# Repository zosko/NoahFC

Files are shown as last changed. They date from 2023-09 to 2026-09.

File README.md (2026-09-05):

# NoahFC
Open Hardware for Smarter Flight

Modular, open-source flight controller with integrated BEC and ESC designs. Build, customize, and fly freely.

#### Based low cost Atmega328 based Flight Controller with necessary features.

# Electronic used
- Flight Controller - [NoahFC](https://github.com/zosko/NoahFC)
- ESC Controller - [NoahESC](https://github.com/zosko/NoahESC)
- BEC - [NoahBEC](https://github.com/zosko/NoahBEC)
- Receiver - (TBS Nano)
- Plane - (ZOHD Drift)
- Camera
- VTX Transmitter

### Features
- [X] **PPM**
- [X] **GPS**
- [X] **Manual mode**
- [X] **Stable mode**
- [X] Return to home
- [X] **OSD**

### Used Pins
Arduino | Component | Arduino | Component
--------|----------|---------|---------
D0| UART RX| D9| Alerons
D1| UART TX| D10 | SS (OSD)
D2| GPS RX | D11 | MOSI (OSD)
D3| PPM Input | D12 | MISO (OSD)
D5| Throttle | D13 | SCK (OSD)
D6| Elevator | SDA | IMU
D8| GPS TX | SCL | IMU

### Transmitter setup
Channel | Info
-----|-----
CH1 | Elevator
CH2 | Alerons
CH3 | Throttle
CH4 | Take off
CH5 | Modes

### Modes
Channel 5 should be 3-position switch
- Min [**Manual**]
- Mid [**Stable**]
- Max [**RTH**]

### Take off
- Channel 4 should be 2-position switch
- Min [**nothing**]
- Max [**Take Off**]

### Firmware
**Download**: [Firmware](firmware.hex)
```
Sketch uses 28472 bytes (92%) of program storage space. Maximum is 30720 bytes.
Global variables use 1267 bytes (61%) of dynamic memory, leaving 781 bytes for local variables. Maximum is 2048 bytes.
```
**Installation**:
`avrdude -p m328 -c arduino -P /dev/ttyUSB0 -b 115200 -F -U flash:w:firmware.hex`

## OSD
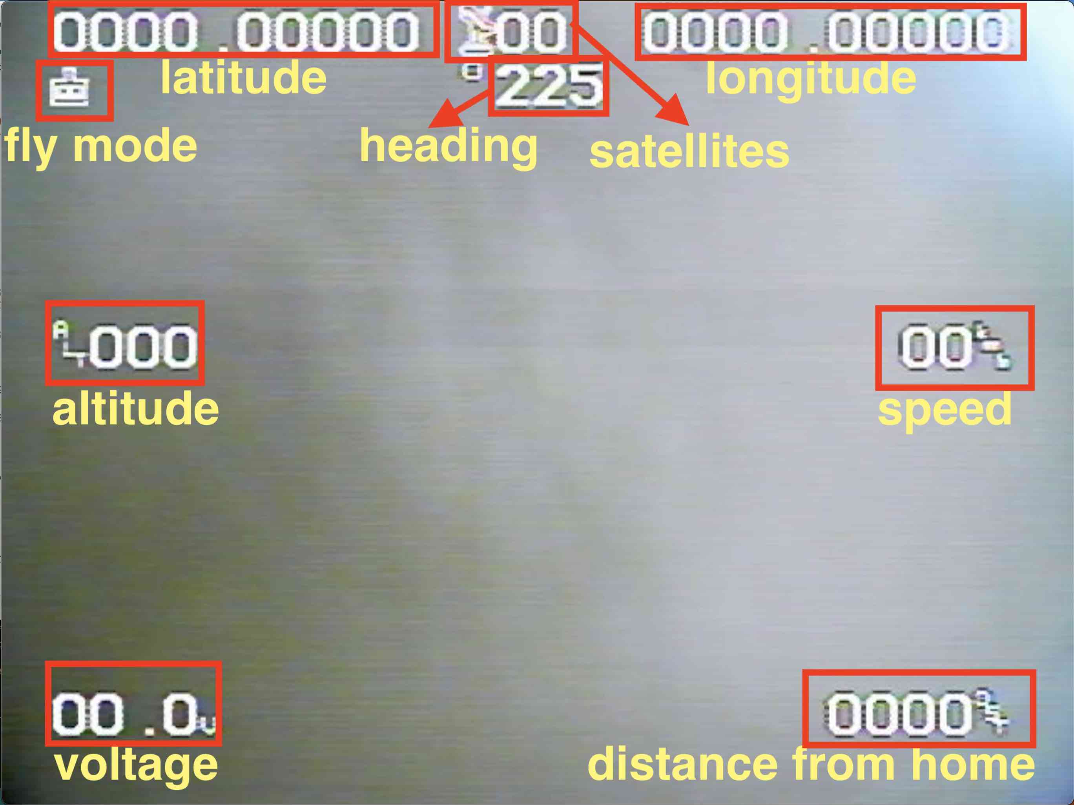
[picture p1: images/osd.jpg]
OSD


## Scheme
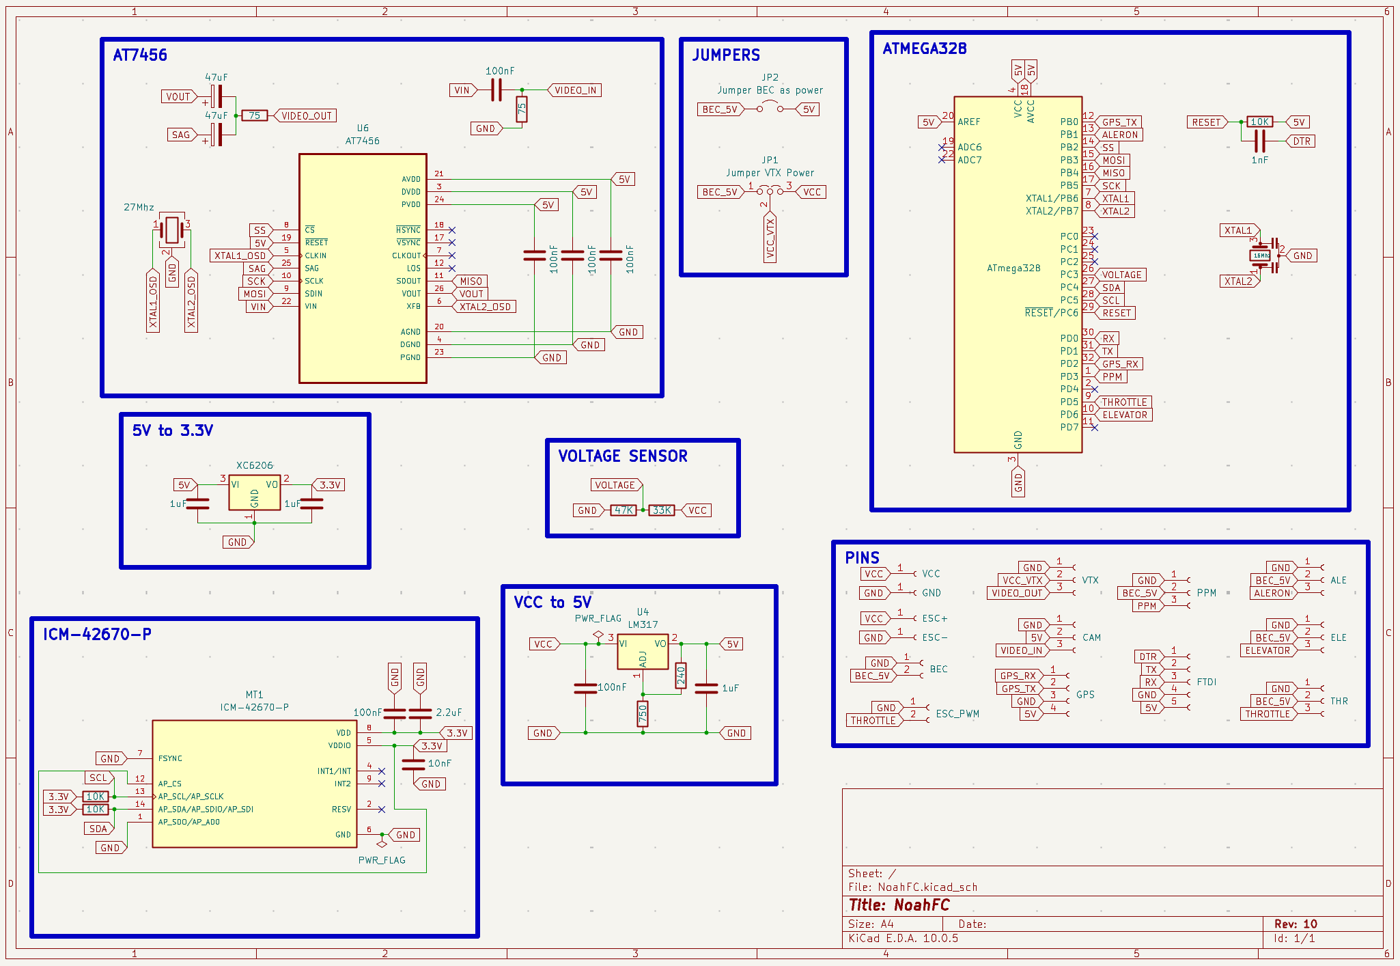
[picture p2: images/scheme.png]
Scheme


## Boards Preview
Board|PCB
---------|---------
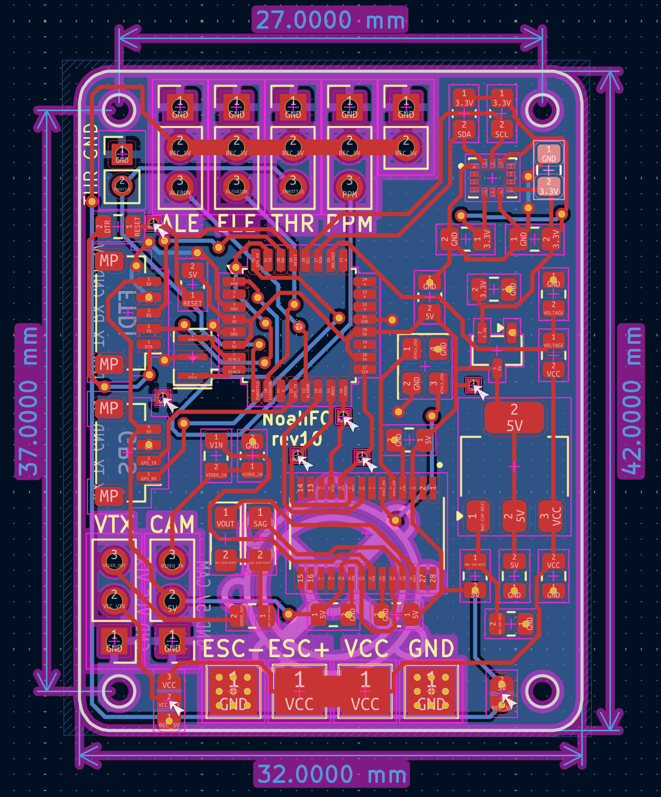
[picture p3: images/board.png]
Board
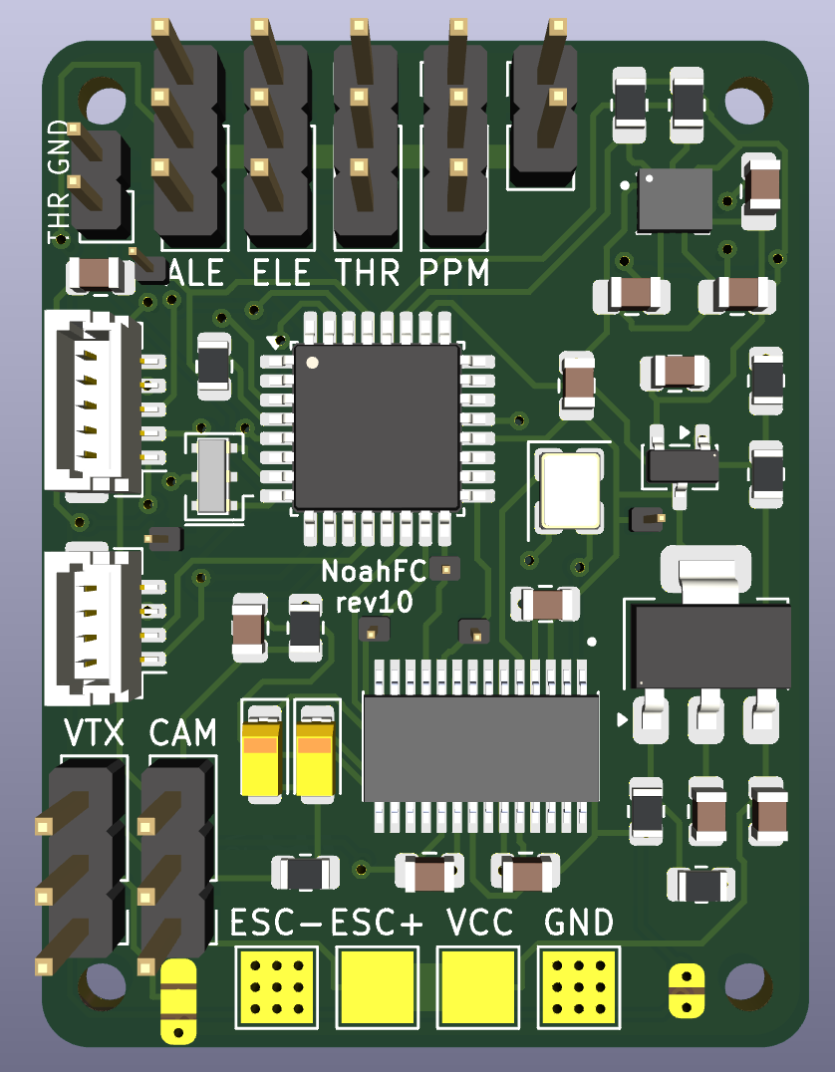
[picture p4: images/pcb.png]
View 1
|

## Sponsorship

PCBWay_logo

**This project is proudly sponsored by [PCBWay](https://pcbway.com).**

PCBWay specializes in manufacturing high-quality printed circuit boards (PCBs), making them accessible and affordable for both hobbyists and professionals.

Their range of services includes:

- PCB prototyping
- Assembly services
- Instant order quotations
- Expert verification processes
- A user-friendly, hassle-free ordering system

I'm sincerely grateful to PCBWay for their generous support in making this project possible.

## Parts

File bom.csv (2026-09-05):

Reference | Value | Qty | LCSC
C1,C2,C4,C5,C13,C17 | 100nF | 6 | C19186128,C49678
C3 | 1nF | 1 | C94121
C10,C11,C12 | 1uF | 3 | C28323
C14 | 10nF | 1 | C49296944
C15 | 2.2uF | 1 | C513763
C18,C19 | 47uF | 2 | C131173
J1 | ALE | 1 | C42431836
J2 | ELE | 1 | C42431836
J3 | VCC | 1
J4 | FTDI | 1 | C160391
J5 | GND | 1
J6 | THR | 1 | C42431836
J7 | PPM | 1 | C42431836
J8 | GPS | 1 | C160390
J9 | ESC+ | 1
J10 | ESC- | 1
J11 | CAM | 1 | C42431836
J12 | VTX | 1 | C42431836
J15 | ESC_PWM | 1 | C7501607
J17 | BEC | 1 | C42431798
JP2 | Jumper BEC as power | 1
MT1 | ICM-42670-P | 1 | C3288646
R1,R3,R6 | 10K | 3 | C84376
R2 | 240 | 1 | C17572
R4 | 47K | 1 | C17713
R5 | 33K | 1 | C2933415
R9,R10 | 75 | 2 | C2974040
R11 | 750 | 1 | C114546
U1 | ATmega328 | 1 | C618731
U3 | XC6206 | 1 | C3015484
U4 | LM317 | 1 | C68487
U6 | AT7456 | 1 | C82351
Y1 | 16Mhz | 1 | C882606
Y3 | 27Mhz | 1 | C5444552

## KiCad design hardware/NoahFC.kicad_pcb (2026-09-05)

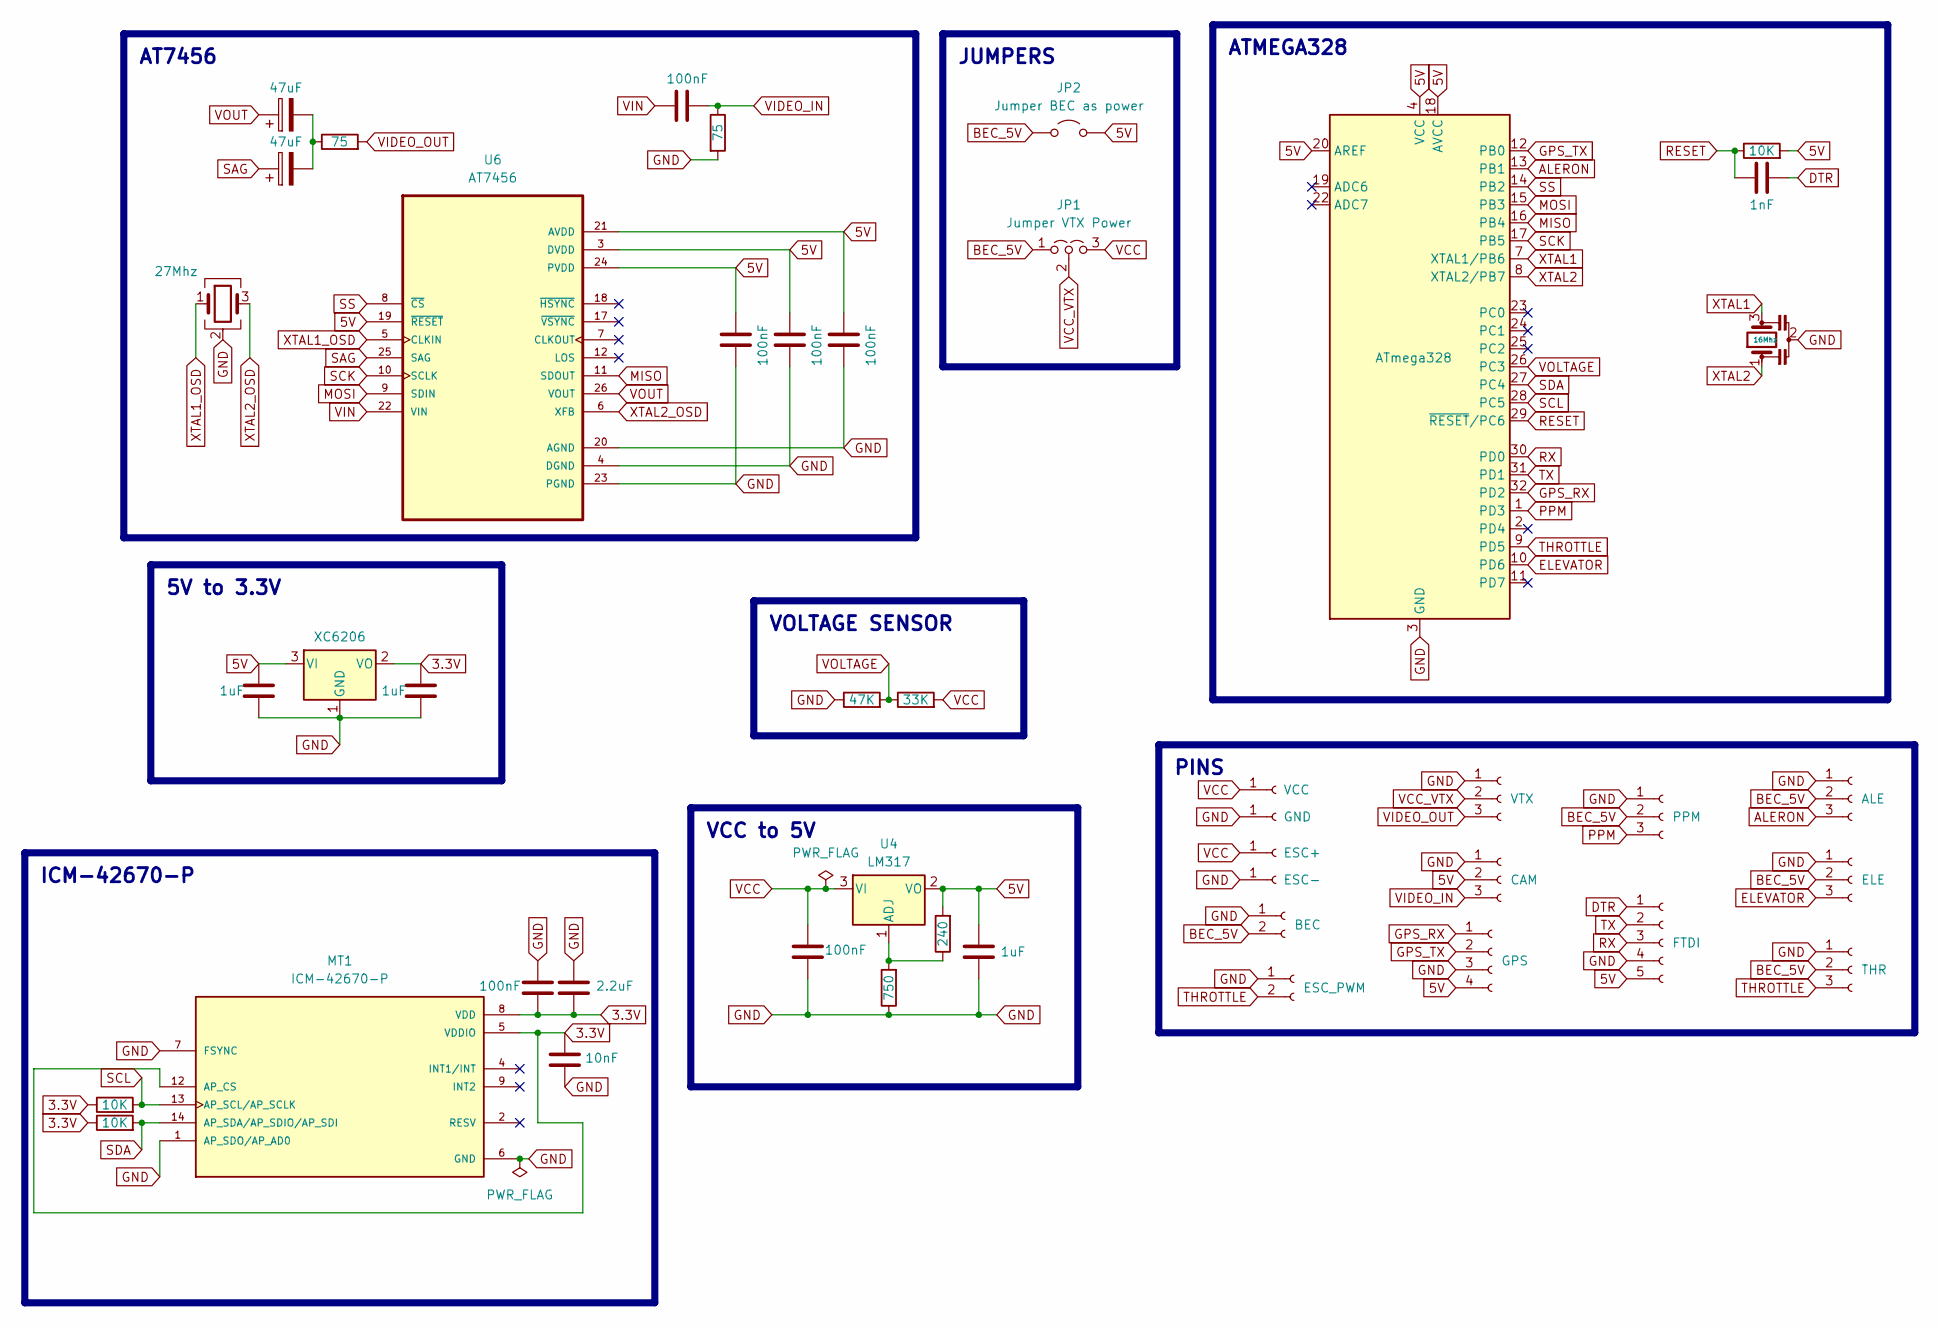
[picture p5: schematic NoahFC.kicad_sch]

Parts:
C1, C2, C4, C5, C17: 100nF; C_0805_2012Metric; LCSC C49678
C3: 1nF; C_0805_2012Metric; LCSC C94121
C10, C11, C12: 1uF; C_0805_2012Metric; LCSC C28323
C13: 100nF; C_0805_2012Metric_Pad1.18x1.45mm_HandSolder; LCSC C19186128
C14: 10nF; C_0805_2012Metric_Pad1.18x1.45mm_HandSolder; LCSC C49296944
C15: 2.2uF; C_0805_2012Metric_Pad1.18x1.45mm_HandSolder; LCSC C513763
C18, C19: 47uF; CP_EIA-3216-18_Kemet-A; LCSC C131173
J1: ALE; PinHeader_1x03_P2.54mm_Vertical; LCSC C42431836
J2: ELE; PinHeader_1x03_P2.54mm_Vertical; LCSC C42431836
J3: VCC; TestPoint_Pad_3.0x3.0mm
J4: FTDI; JST_SH_BM05B-SRSS-TB_1x05-1MP_P1.00mm_Vertical; LCSC C160391
J5: GND; TestPoint_Pad_3.0x3.0mm
J6: THR; PinHeader_1x03_P2.54mm_Vertical; LCSC C42431836
J7: PPM; PinHeader_1x03_P2.54mm_Vertical; LCSC C42431836
J8: GPS; JST_SH_BM04B-SRSS-TB_1x04-1MP_P1.00mm_Vertical; LCSC C160390
J9: ESC+; TestPoint_Pad_3.0x3.0mm
J10: ESC-; TestPoint_Pad_3.0x3.0mm
J11: CAM; PinHeader_1x03_P2.54mm_Vertical; LCSC C42431836
J12: VTX; PinHeader_1x03_P2.54mm_Vertical; LCSC C42431836
J15: ESC_PWM; PinHeader_1x02_P2.00mm_Vertical; LCSC C7501607
J17: BEC; PinHeader_1x02_P2.54mm_Vertical; LCSC C42431798
JP1: Jumper VTX Power; SolderJumper-3_P1.3mm_Open_RoundedPad1.0x1.5mm
JP2: Jumper BEC as power; SolderJumper-2_P1.3mm_Open_RoundedPad1.0x1.5mm
MT1: ICM-42670-P; XDCR_ICM-42670-P; LCSC C3288646
R1: 10K; R_0805_2012Metric; LCSC C84376
R2: 240; R_0805_2012Metric; LCSC C17572
R3, R6: 10K; R_0805_2012Metric_Pad1.20x1.40mm_HandSolder; LCSC C84376
R4: 47K; R_0805_2012Metric; LCSC C17713
R5: 33K; R_0805_2012Metric; LCSC C2933415
R9, R10: 75; R_0805_2012Metric; LCSC C2974040
R11: 750; R_0805_2012Metric; LCSC C114546
U1: ATmega328; TQFP-32_7x7mm_P0.8mm; LCSC C618731
U3: XC6206; SOT-23-3; LCSC C3015484
U4: LM317; SOT-223-3_TabPin2; LCSC C68487
U6: AT7456; SOP65P637X110-28N; LCSC C82351
Y1: 16Mhz; Resonator_SMD_Murata_CSTxExxV-3Pin_3.0x1.1mm; LCSC C882606
Y3: 27Mhz; Crystal_SMD_3225-4Pin_3.2x2.5mm; LCSC C5444552

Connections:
3.3V: C11.2, C13.2, C14.1, C15.2, MT1.5 (VDDIO), MT1.8 (VDD), MT1.12 (AP_CS), R3.1, R6.1, U3.2 (VO)
5V: C1.1, C2.1, C4.1, C10.2, C12.2, J4.5, J8.4, J11.2, JP2.2 (B), R1.2, R2.2, U1.4 (VCC), U1.6 (VCC), U1.18 (AVCC), U1.20 (AREF), U3.3 (VI), U4.2 (VO), U6.3 (DVDD), U6.19 (~RESET), U6.21 (AVDD), U6.24 (PVDD)
ALERON: J1.3, U1.13 (PB1)
BEC_5V: J1.2, J2.2, J6.2, J7.2, J17.2, JP1.1 (A), JP2.1 (A)
DTR: C3.2, J4.1
ELEVATOR: J2.3, U1.10 (PD6)
GND: C1.2, C2.2, C4.2, C5.1, C10.1, C11.1, C12.1, C13.1, C14.2, C15.1, J1.1, J2.1, J4.4, J5.1 (Pin_1_1), J6.1, J7.1, J8.3, J10.1 (Pin_1_1), J11.1, J12.1, J15.1, J17.1, MT1.1 (AP_SDO/AP_AD0), MT1.6 (GND), MT1.7 (FSYNC), R4.1, R9.2, R11.1, U1.3 (GND), U1.5 (GND), U1.21 (GND), U3.1 (GND), U6.4 (DGND), U6.20 (AGND), U6.23 (PGND), Y1.2, Y3.2 (G), Y3.4 (G)
GPS_RX: J8.1, U1.32 (PD2)
GPS_TX: J8.2, U1.12 (PB0)
MISO: U1.16 (PB4), U6.11 (SDOUT)
MOSI: U1.15 (PB3), U6.9 (SDIN)
unnamed: C18.2, C19.2, R10.1
unnamed: R2.1, R11.2, U4.1 (ADJ)
PPM: J7.3, U1.1 (PD3)
RESET: C3.1, R1.1, U1.29 (~RESET/PC6)
RX: J4.3, U1.30 (PD0)
SAG: C19.1, U6.25 (SAG)
SCK: U1.17 (PB5), U6.10 (SCLK)
SCL: MT1.13 (AP_SCL/AP_SCLK), R3.2, U1.28 (PC5)
SDA: MT1.14 (AP_SDA/AP_SDIO/AP_SDI), R6.2, U1.27 (PC4)
SS: U1.14 (PB2), U6.8 (~CS)
THROTTLE: J6.3, J15.2, U1.9 (PD5)
TX: J4.2, U1.31 (PD1)
VCC: C5.2, J3.1 (Pin_1_1), J9.1 (Pin_1_1), JP1.3 (B), R5.2, U4.3 (VI)
VCC_VTX: J12.2, JP1.2 (C)
VIDEO_IN: C17.2, J11.3, R9.1
VIDEO_OUT: J12.3, R10.2
VIN: C17.1, U6.22 (VIN)
VOLTAGE: R4.2, R5.1, U1.26 (PC3)
VOUT: C18.1, U6.26 (VOUT)
XTAL1: U1.7 (XTAL1/PB6), Y1.3
XTAL1_OSD: U6.5 (CLKIN), Y3.1
XTAL2: U1.8 (XTAL2/PB7), Y1.1
XTAL2_OSD: U6.6 (XFB), Y3.3

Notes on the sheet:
JUMPERS
ATMEGA328
AT7456
VCC to 5V
5V to 3.3V
VOLTAGE SENSOR
ICM-42670-P
PINS

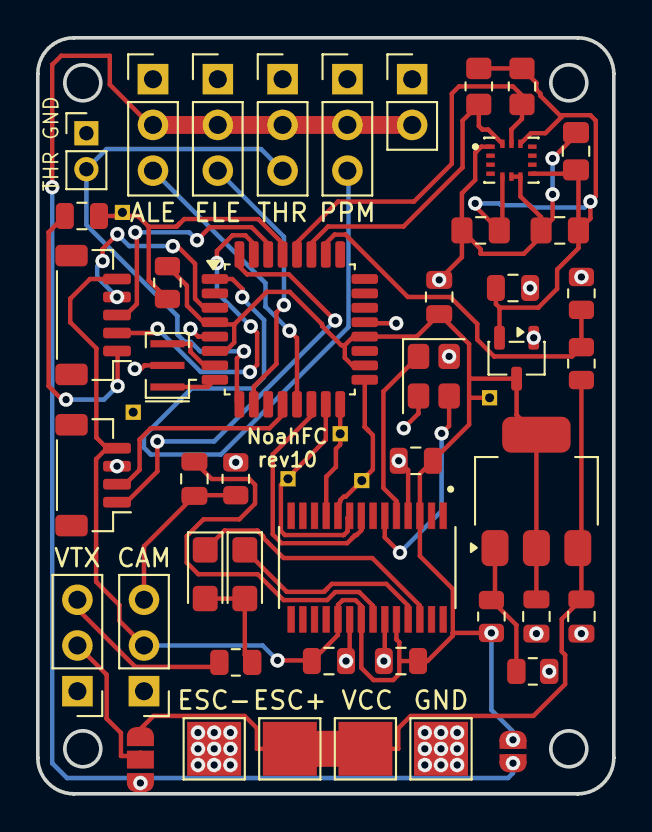
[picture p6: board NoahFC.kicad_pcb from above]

Board: 2 copper layers, 32.0 x 42.0 mm, 46 parts (0 on the bottom side), 34 nets.

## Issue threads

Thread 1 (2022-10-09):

Can RP2040 be supported?

01Space, 2022-10-09:
Your project is great! I'm very interested. I want to migrate your code to RP2040. What is the current step of your project? I'm looking forward to the GPS home function

zosko, 2022-10-10:
Hey, firmware is for rev1 PCB board and still ground test is working good, i want to make few tests in the sky soon as possible. Meantime i order boards for rev2 . I have teoreticly RTH coded but i did not  test that still. Its not good idea now to migrate code because is not fully tested. I will let you know when is ready.

01Space, 2022-10-16:
thank you!

I like the iNavTelemetry project very much.

Closed 2023-08-21.

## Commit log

2022-04-13 separate panel board
    [NoahFC_panel.kicad_pcb]
2022-05-07 revision 1
    [NoahFC.kicad_pcb, NoahFC.kicad_sch]
2022-05-17 pin mapping
2022-05-19 remove one aleron servo
    [NoahFC.kicad_pcb, NoahFC.kicad_sch]
2022-05-19 include servoTimer
2022-05-27 route board
    [NoahFC.kicad_pcb, NoahFC.kicad_sch]
2022-05-28 rev1 updates
    [NoahFC.kicad_pcb, NoahFC.kicad_sch]
2022-05-28 pin improve
    [NoahFC.kicad_pcb, NoahFC.kicad_sch]
2022-05-30 fill board
    [NoahFC.kicad_pcb, NoahFC_panel.kicad_pcb]
2022-06-30 gps pin correction
2022-06-30 add voltage in debug
2022-06-30 add leds funcs
2022-06-30 add correction in voltage read
2022-06-30 add RESET pad
    [NoahFC.kicad_pcb, NoahFC.kicad_sch]
2022-07-27 add rev2 version board
    [NoahFC.kicad_pcb, NoahFC.kicad_sch]
2022-07-29 add board rev2 image
2022-07-29 update scheme / design and board
    [NoahFC.kicad_pcb, NoahFC.kicad_sch, NoahFC_panel.kicad_pcb]
2022-07-30 redesign board
    [NoahFC.kicad_pcb, NoahFC.kicad_sch]
2022-07-30 remove panel
    [NoahFC_panel.kicad_pcb]
2022-08-03 tidy board
    [NoahFC.kicad_pcb, NoahFC.kicad_sch]
2022-08-08 rename folder
    [NoahFC.kicad_pcb, NoahFC.kicad_sch]
2022-08-20 kalman filter
2022-08-21 route rev2
    [NoahFC.kicad_pcb]
2022-10-01 small tidy in firmware
    [NoahFC.kicad_pcb, NoahFC.kicad_sch]
2022-12-22 add experimental revision
    [NoahFC.kicad_pcb, NoahFC.kicad_sch]
2022-12-22 add images
    [NoahFC.kicad_pcb, NoahFC.kicad_sch]
2023-09-07 rev4 project
    [NoahFC.kicad_pcb, NoahFC.kicad_sch]
2023-09-28 removed experimental version
    [NoahFC.kicad_pcb, NoahFC.kicad_sch]
2023-09-28 add bottom labels
    [NoahFC.kicad_pcb, NoahFC.kicad_sch]
2023-11-14 update project rev5
    [NoahFC.kicad_pcb, NoahFC.kicad_sch]
2023-11-19 edit footprint
2023-11-19 add sda scl pinout
    [NoahFC.kicad_pcb, NoahFC.kicad_sch]
2023-11-28 add jumper, organize pcb
    [NoahFC.kicad_pcb, NoahFC.kicad_sch]
2023-11-28 new images with organized pcb with jumper
2023-11-30 gerbers path
    [NoahFC.kicad_pcb]
2024-02-28 update to kicad 8
    [NoahFC.kicad_pcb, NoahFC.kicad_sch]
2024-03-05 rev6 project
    [NoahFC.kicad_sch]
2024-03-05 add missing board file
    [NoahFC.kicad_pcb]
2024-04-20 reworked rev6 - experimental
    [NoahFC.kicad_pcb, NoahFC.kicad_sch]
2024-07-06 add silk
    [NoahFC.kicad_pcb, NoahFC.kicad_sch]
2024-07-06 proj file update
    [NoahFC.kicad_pcb]
2024-07-29 replace buck converter with LM317
    [NoahFC.kicad_pcb, NoahFC.kicad_sch]
2025-07-31 update to rev7 board
    [NoahFC.kicad_pcb, NoahFC.kicad_sch]
2025-08-01 remove unused pin
2025-10-25 increaes line
    [NoahFC.kicad_pcb]
2025-11-30 add bom file
    [bom.csv]
2025-11-30 update project with LCSC parts, fix some component prepare rev8
    [NoahFC.kicad_pcb, NoahFC.kicad_sch]
2025-12-21 added 5V jumper for BEC
    [NoahFC.kicad_pcb]
2026-04-07 add jumpers for vtx
    [NoahFC.kicad_pcb, NoahFC.kicad_sch]
